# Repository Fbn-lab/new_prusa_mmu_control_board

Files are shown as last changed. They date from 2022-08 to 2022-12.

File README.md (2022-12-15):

(语言 language) : [CN](https://github.com/fBn0523/new_prusa_mmu_control_board/blob/main/README.md)|[EN](https://github.com/fBn0523/new_prusa_mmu_control_board/blob/main/README_EN.md)

# ENDER3多色改装方案
# new_prusa_mmu_hardware
平替原版mmu2主板,单板只需要约100(CNY)\
  PCB_V4.1|参数|类型
  --------|---|---
  电源|12~24V|/
  串口|5V/3.3V|/
  FINDA传感器|12~24V|三线PNP常开
电机驱动|/|TMC2130

直插mks主板，兼容更多打印机。\
无论你的打印机是否来自prusa生产，只要主板拥有一个空闲的串口和两个gpio,使用marlin固件。都可以使用mmu换料器。
# image
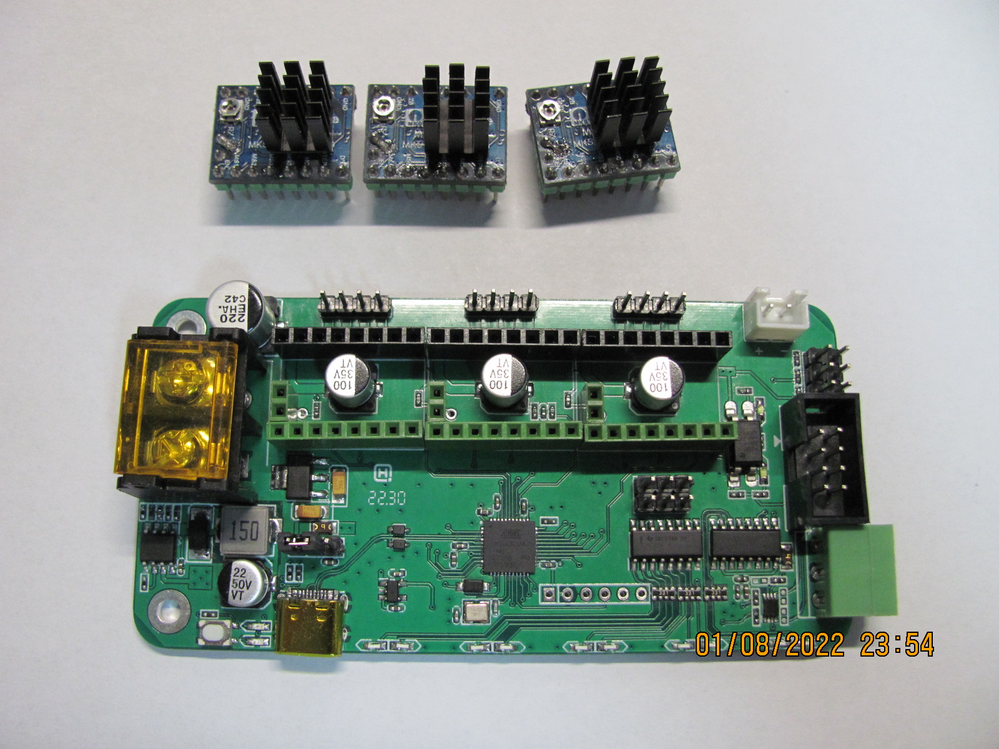
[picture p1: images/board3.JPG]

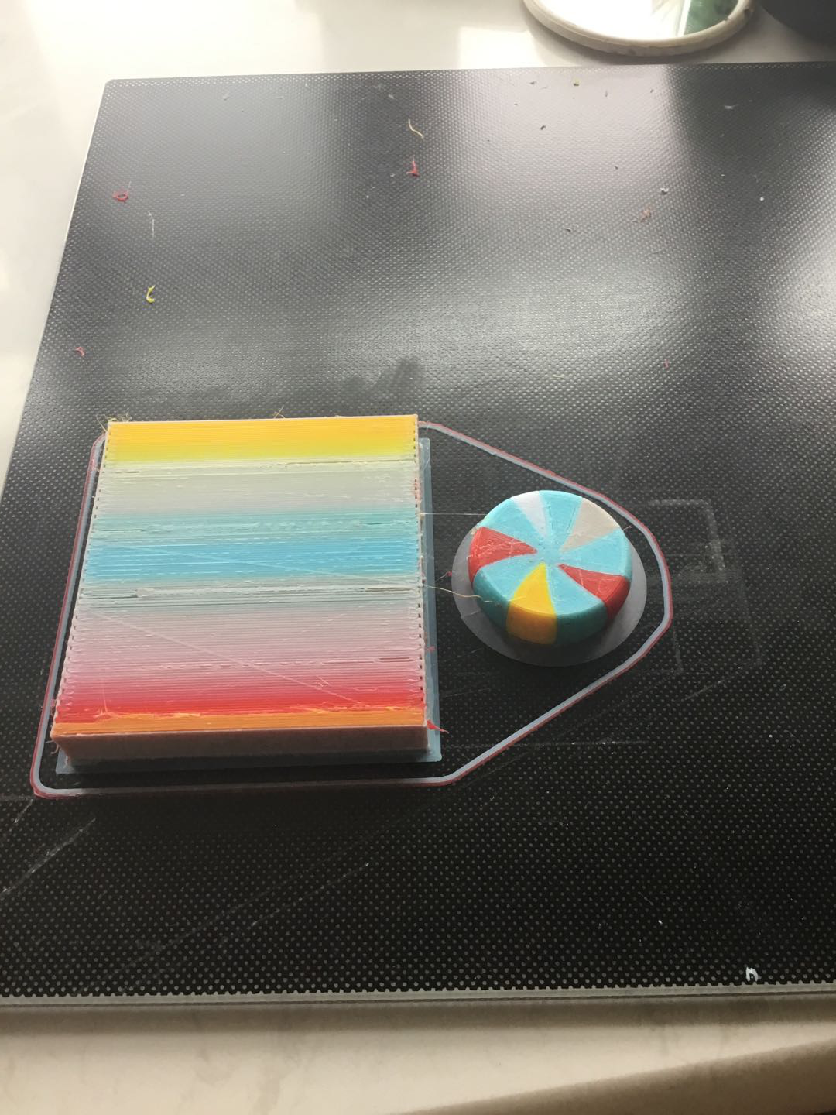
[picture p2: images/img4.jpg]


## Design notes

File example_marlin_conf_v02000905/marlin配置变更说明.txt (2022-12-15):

/**********************************************************************/
#define EXTRUDERS 5//部分主板不能设置5个挤出机,忽略错误即可
/**********************************************************************/
#define MMU_MODEL PRUSA_MMU2   
/**********************************************************************/
#define FILAMENT_RUNOUT_SENSOR  //断料传感器使能
#if ENABLED(FILAMENT_RUNOUT_SENSOR)
  #define FIL_RUNOUT_ENABLED_DEFAULT true 
  #define NUM_RUNOUT_SENSORS   1           

  #define FIL_RUNOUT_STATE     HIGH        
  #define FIL_RUNOUT_PULLUP       
/**********************************************************************/

#define NOZZLE_PARK_FEATURE//用于设置mmu停止时喷头位置

#if ENABLED(NOZZLE_PARK_FEATURE)
  // Specify a park position as { X, Y, Z_raise }
  #define NOZZLE_PARK_POINT { (X_MIN_POS + 10), (Y_MIN_POS + 10), 20 }
  #define NOZZLE_PARK_MOVE          0   // Park motion: 0 = XY Move, 1 = X Only, 2 = Y Only, 3 = X before Y, 4 = Y before X
  #define NOZZLE_PARK_Z_RAISE_MIN   2   // (mm) Always raise Z by at least this distance
  #define NOZZLE_PARK_XY_FEEDRATE 100   // (mm/s) X and Y axes feedrate (also used for delta Z axis)
  #define NOZZLE_PARK_Z_FEEDRATE    5   // (mm/s) Z axis feedrate (not used for delta printers)
#endif       

#define ADVANCED_PAUSE_FEATURE//多色上下料速度长度设置
#if ENABLED(ADVANCED_PAUSE_FEATURE)
  #define PAUSE_PARK_RETRACT_FEEDRATE         60  // (mm/s) Initial retract feedrate.
  #define PAUSE_PARK_RETRACT_LENGTH            2  // (mm) Initial retract.
                                                  // This short retract is done immediately, before parking the nozzle.
  #define FILAMENT_CHANGE_UNLOAD_FEEDRATE     10  // (mm/s) Unload filament feedrate. This can be pretty fast.
  #define FILAMENT_CHANGE_UNLOAD_ACCEL        25  // (mm/s^2) Lower acceleration may allow a faster feedrate.
  #define FILAMENT_CHANGE_UNLOAD_LENGTH      100  // (mm) The length of filament for a complete unload.
                                                  //   For Bowden, the full length of the tube and nozzle.
                                                  //   For direct drive, the full length of the nozzle.
                                                  //   Set to 0 for manual unloading.
  #define FILAMENT_CHANGE_SLOW_LOAD_FEEDRATE   6  // (mm/s) Slow move when starting load.
  #define FILAMENT_CHANGE_SLOW_LOAD_LENGTH     0  // (mm) Slow length, to allow time to insert material.
                                                  // 0 to disable start loading and skip to fast load only
  #define FILAMENT_CHANGE_FAST_LOAD_FEEDRATE   6  // (mm/s) Load filament feedrate. This can be pretty fast.
  #define FILAMENT_CHANGE_FAST_LOAD_ACCEL     25  // (mm/s^2) Lower acceleration may allow a faster feedrate.
  #define FILAMENT_CHANGE_FAST_LOAD_LENGTH    90  // (mm) Load length of filament, from extruder gear to nozzle.
                                                  //   For Bowden, the full length of the tube and nozzle.
                                                  //   For direct drive, the full length of the nozzle.
  //#define ADVANCED_PAUSE_CONTINUOUS_PURGE       // Purge continuously up to the purge length until interrupted.
  #define ADVANCED_PAUSE_PURGE_FEEDRATE        3  // (mm/s) Extrude feedrate (after loading). Should be slower than load feedrate.
  #define ADVANCED_PAUSE_PURGE_LENGTH         25  // (mm) Length to extrude after loading.
                                                  //   Set to 0 for manual extrusion.
                                                  //   Filament can be extruded repeatedly from the Filament Change menu
                                                  //   until extrusion is consistent, and to purge old filament.
  #define ADVANCED_PAUSE_RESUME_PRIME          0  // (mm) Extra distance to prime nozzle after returning from park.
  //#define ADVANCED_PAUSE_FANS_PAUSE             // Turn off print-cooling fans while the machine is paused.

                                                  // Filament Unload does a Retract, Delay, and Purge first:
  #define FILAMENT_UNLOAD_PURGE_RETRACT       13  // (mm) Unload initial retract length.
  #define FILAMENT_UNLOAD_PURGE_DELAY       5000  // (ms) Delay for the filament to cool after retract.
  #define FILAMENT_UNLOAD_PURGE_LENGTH         8  // (mm) An unretract is done, then this length is purged.
  #define FILAMENT_UNLOAD_PURGE_FEEDRATE      25  // (mm/s) feedrate to purge before unload

  #define PAUSE_PARK_NOZZLE_TIMEOUT           45  // (seconds) Time limit before the nozzle is turned off for safety.
  #define FILAMENT_CHANGE_ALERT_BEEPS         10  // Number of alert beeps to play when a response is needed.
  #define PAUSE_PARK_NO_STEPPER_TIMEOUT           // Enable for XYZ steppers to stay powered on during filament change.
  //#define FILAMENT_CHANGE_RESUME_ON_INSERT      // Automatically continue / load filament when runout sensor is triggered again.
  //#define PAUSE_REHEAT_FAST_RESUME              // Reduce number of waits by not prompting again post-timeout before continuing.

  //#define PARK_HEAD_ON_PAUSE                    // Park the nozzle during pause and filament change.
  //#define HOME_BEFORE_FILAMENT_CHANGE           // If needed, home before parking for filament change

  #define FILAMENT_LOAD_UNLOAD_GCODES           // Add M701/M702 Load/Unload G-codes, plus Load/Unload in the LCD Prepare menu.
  //#define FILAMENT_UNLOAD_ALL_EXTRUDERS         // Allow M702 to unload all extruders above a minimum target temp (as set by M302)
#endif 
/**********************************************************************/
/**
 * Průša Multi-Material Unit (MMU)
 * Enable in Configuration.h
 *
 * These devices allow a single stepper driver on the board to drive
 * multi-material feeders with any number of stepper motors.
 */
#if HAS_PRUSA_MMU1
  /**
   * This option only allows the multiplexer to switch on tool-change.
   * Additional options to configure custom E moves are pending.
   *
   * Override the default DIO selector pins here, if needed.
   * Some pins files may provide defaults for these pins.
   */
  //#define E_MUX0_PIN 40  // Always Required
  //#define E_MUX1_PIN 42  // Needed for 3 to 8 inputs
  //#define E_MUX2_PIN 44  // Needed for 5 to 8 inputs
#elif HAS_PRUSA_MMU2
  // Serial port used for communication with MMU2.
  #define MMU2_SERIAL Serial2//串口号 (BOARD_TRIGORILLA_13 选串口3)(MKS tinybee选串口二)

  // Use hardware reset for MMU if a pin is defined for it
  #define MMU2_RST_PIN 2//复位引脚

  // Enable if the MMU2 has 12V stepper motors (MMU2 Firmware 1.0.2 and up)
  #define MMU2_MODE_12V//供电是否12V

  // G-code to execute when MMU2 F.I.N.D.A. probe detects filament runout
  #define MMU2_FILAMENT_RUNOUT_SCRIPT "M600"

  // Add an LCD menu for MMU2
  #define MMU2_MENUS
  #if EITHER(MMU2_MENUS, HAS_PRUSA_MMU2S)
    // Settings for filament load / unload from the LCD menu.
    // This is for Průša MK3-style extruders. Customize for your hardware.
    #define MMU2_FILAMENTCHANGE_EJECT_FEED 80.0
    #define MMU2_LOAD_TO_NOZZLE_SEQUENCE \
      {  7.2, 1145 }, \
      { 14.4,  871 }, \
      { 36.0, 1393 }, \
      { 14.4,  871 }, \
      { 50.0,  198 }

    #define MMU2_RAMMING_SEQUENCE \
      {   1.0, 1000 }, \
      {   1.0, 1500 }, \
      {   2.0, 2000 }, \
      {   1.5, 3000 }, \
      {   2.5, 4000 }, \
      { -15.0, 5000 }, \
      { -14.0, 1200 }, \
      {  -6.0,  600 }, \
      {  10.0,  700 }, \
      { -10.0,  400 }, \
      { -50.0, 2000 }
  #endif

  /**
   * Using a sensor like the MMU2S
   * This mode requires a MK3S extruder with a sensor at the extruder idler, like the MMU2S.
   * See https://help.prusa3d.com/en/guide/3b-mk3s-mk2-5s-extruder-upgrade_41560, step 11
   */
  #if HAS_PRUSA_MMU2S
    #define MMU2_C0_RETRY   5             // Number of retries (total time = timeout*retries)

    #define MMU2_CAN_LOAD_FEEDRATE 500    // (mm/min)
    #define MMU2_CAN_LOAD_SEQUENCE \
      {  0.1, MMU2_CAN_LOAD_FEEDRATE }, \
      {  50, MMU2_CAN_LOAD_FEEDRATE }, \
      { -42.0, MMU2_CAN_LOAD_FEEDRATE }

    #define MMU2_CAN_LOAD_RETRACT   6.0   // (mm) Keep under the distance between Load Sequence values
    #define MMU2_CAN_LOAD_DEVIATION 0.8   // (mm) Acceptable deviation

    #define MMU2_CAN_LOAD_INCREMENT 0.2   // (mm) To reuse within MMU2 module
    #define MMU2_CAN_LOAD_INCREMENT_SEQUENCE \
      { -MMU2_CAN_LOAD_INCREMENT, MMU2_CAN_LOAD_FEEDRATE }

  #else

    /**
     * MMU1 Extruder Sensor
     *
     * Support for a Průša (or other) IR Sensor to detect filament near the extruder
     * and make loading more reliable. Suitable for an extruder equipped with a filament
     * sensor less than 38mm from the gears.
     *
     * During loading the extruder will stop when the sensor is triggered, then do a last
     * move up to the gears. If no filament is detected, the MMU2 can make some more attempts.
     * If all attempts fail, a filament runout will be triggered.
     */
    #define MMU_EXTRUDER_SENSOR
    #if ENABLED(MMU_EXTRUDER_SENSOR)
      #define MMU_LOADING_ATTEMPTS_NR 5 // max. number of attempts to load filament if first load fail
    #endif

  #endif

  //#define MMU2_DEBUG  // Write debug info to serial output

#endif // HAS_PRUSA_MMU2

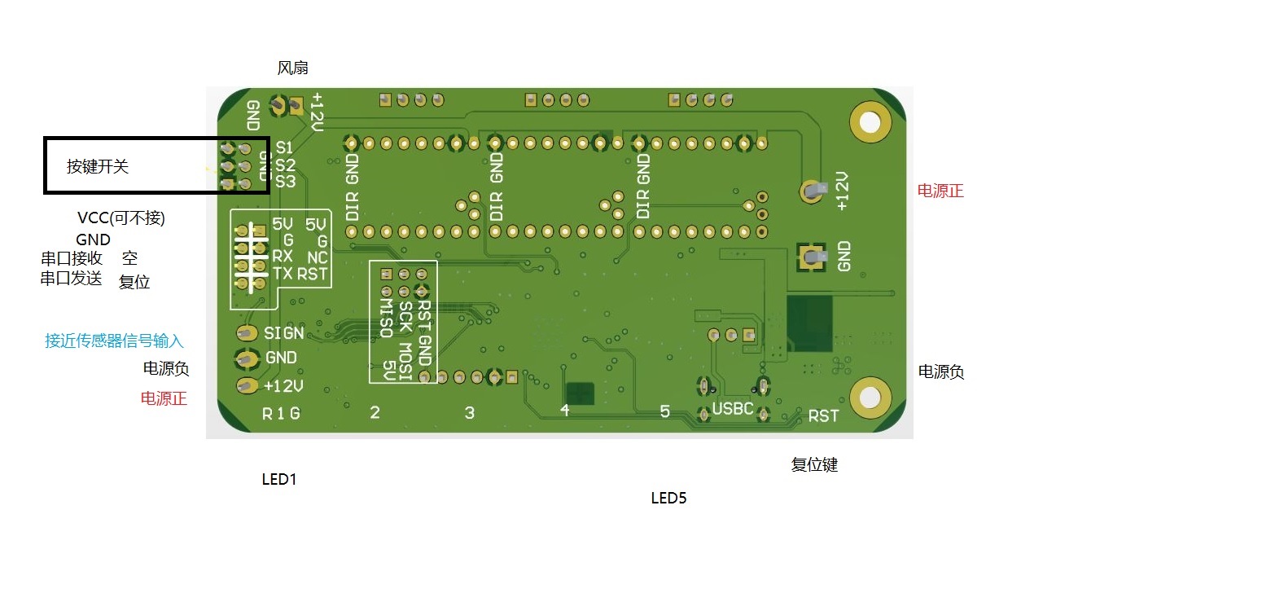
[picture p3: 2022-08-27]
hardware/mother_board/板卡底面示意图.JPG

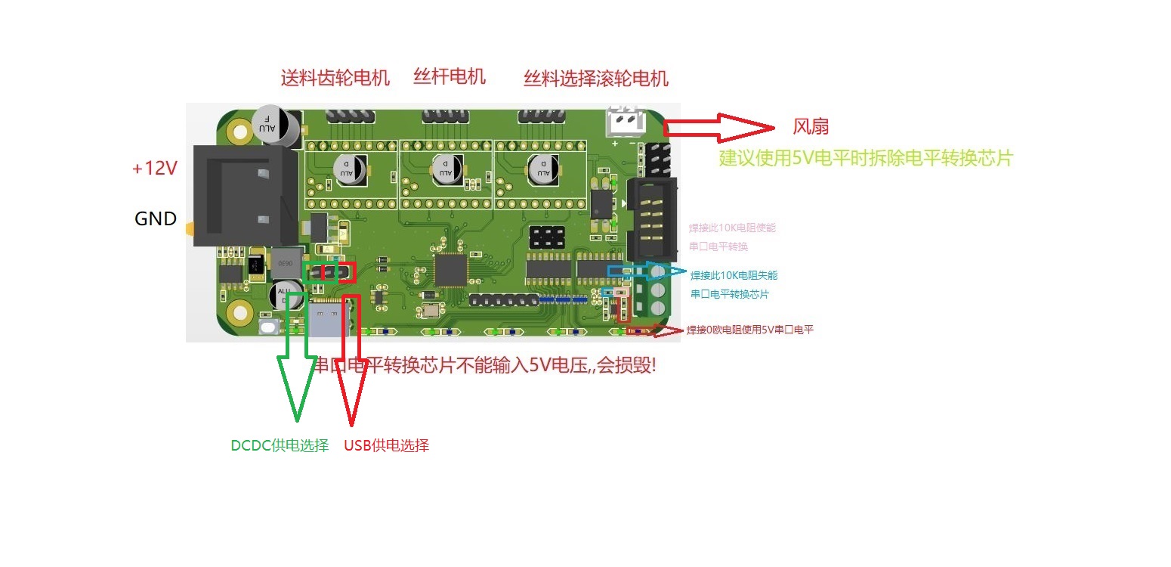
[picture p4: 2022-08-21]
hardware/mother_board/接线示意图_V3.4_HQPCB__20_30.jpg

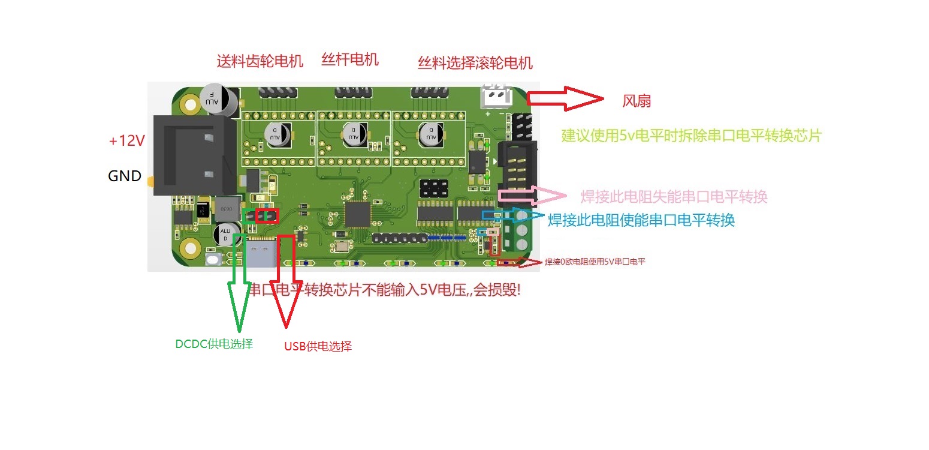
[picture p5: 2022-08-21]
hardware/mother_board/接线示意图_V4.1.jpg

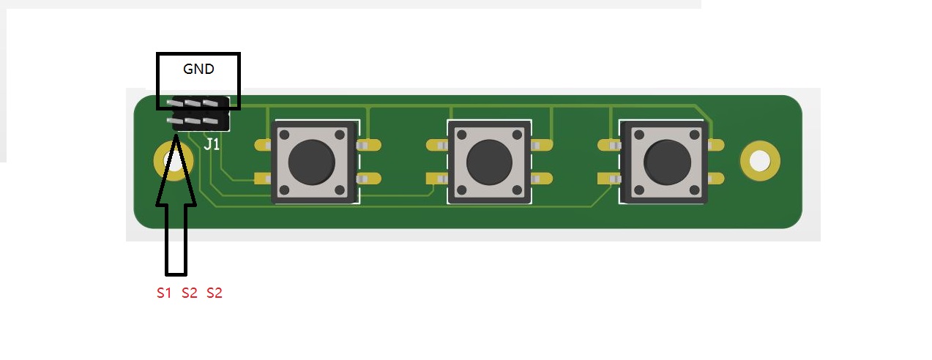
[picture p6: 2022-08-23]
hardware/switch_board/接线示意图.JPG

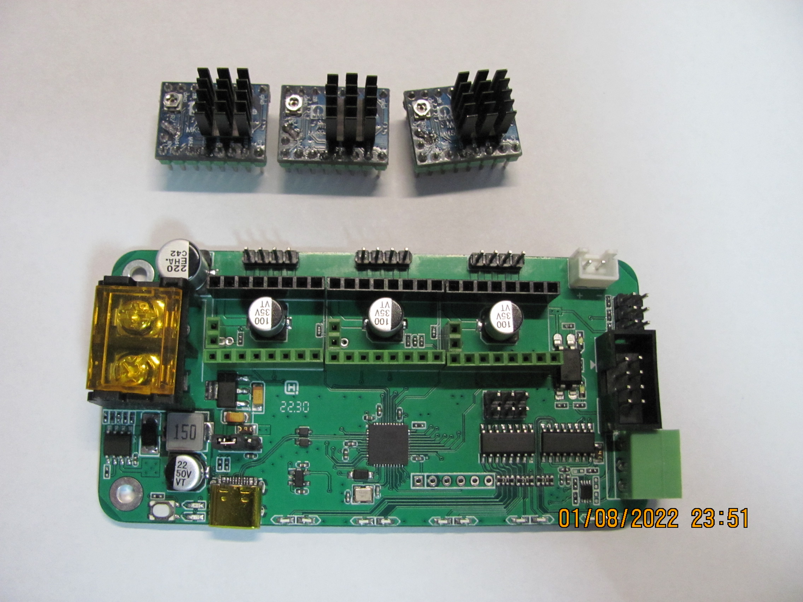
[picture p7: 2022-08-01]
images/board2.JPG

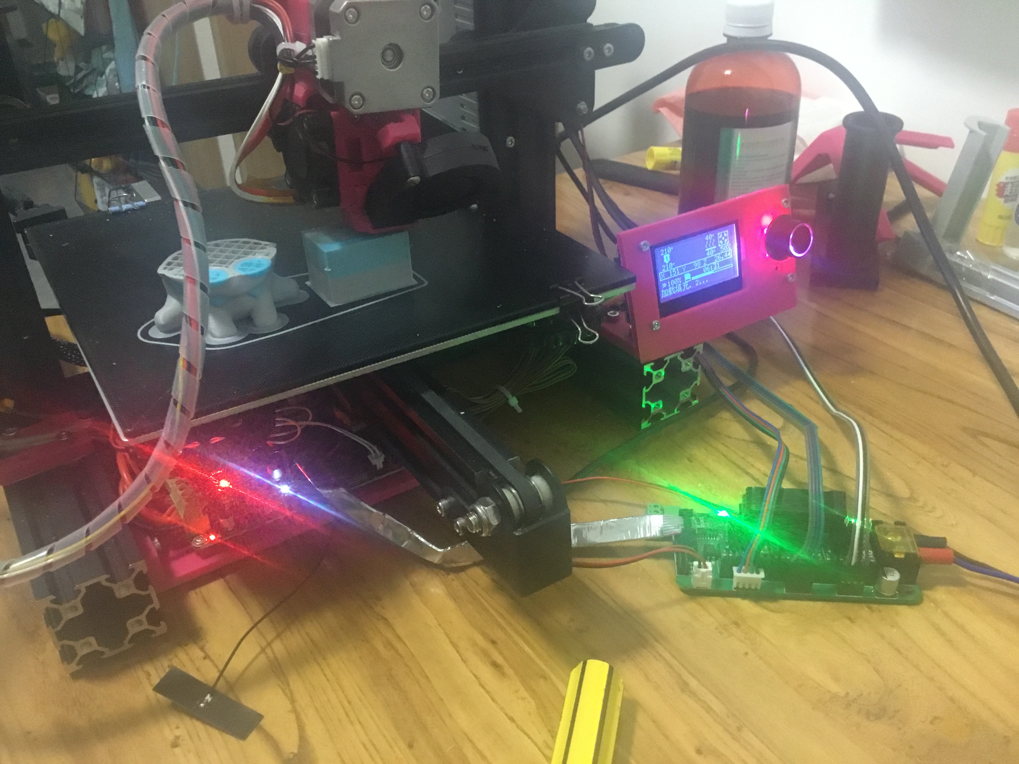
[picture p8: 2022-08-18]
images/img.jpg

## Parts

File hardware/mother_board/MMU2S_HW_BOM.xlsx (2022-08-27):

Comment | 厂家 | 立创商城产品号 | Description | 元件号 | 封装 | LibRef | 数量 | 特别注意连接器间距,电容耐压.器件高温性能
10uF |  |  | 无极性电容 | C1, C10, C12, C14 | 0402C | CAP | 4
100nF |  |  | 无极性电容 | C2, C4, C7, C9, C11, C13, C15 | 0402C | CAP | 7
150pF |  |  | 无极性电容 | C3 | 0402C | CAP | 1
1uF |  |  | 无极性电容 | C5, C16, C17 | 0402C | CAP | 3
12pF |  |  | 无极性电容 | C6, C8 | 0402C | CAP | 2
SS34 | 萨科微 | C77336 | 肖特基二极管 | D1 | SMA/DO-214AC | DIODE SCHOTTKY | 1
LED |  |  | LED灯 | D2,D3,D4,D5,D6,D7,D8, D9, D10, D11,D12,D13 D14, D16, | LED-0603 | 注意颜色！ | 14
DIODE | 杨杰 | C961806 | 普通二极管 | D15 | SOD-123 | DIODE | 1
SMBJ5 | 美台 | C460454 | TVS二极管5V | D17, D18 | SOD-323 | DIODE ZENER | 2
100uF | 建议车规级,耐高温 |  | 贴片电解电容 | EC1, EC2, EC3 | SMD-EC6.3X6.3X10 | SMD_ECAP | 3
22uF |  |  | 贴片电解电容 | EC4 | SMD-EC6.3X6.3X10 | SMD_ECAP | 1
220uF | Panasonic | C336329 | 贴片电解电容 | EC5 | SMD-EC8X8X10 | SMD_ECAP | 1
ATMEGA32U4RC-MU | microchip |  | 单片机 | IC1 | QFN50P700X700X100-45N-D | ATMEGA32U4RC-MU | 1
74HC595D | Ti |  | 8位移位寄存器 | IC2, IC3 | SOIC127P600X175-16N | 74HC595D | 2
MP1584EN-LF |  |  | DCDC芯片 | IC4 | SOIC127P600X170-9N | MP1584EN-LF | 1
AMS1117-5 | UMW | C347223 | 低压差线性稳压器LDO | IC5 | SOT229P700X180-4N | AMS1117 | 1
ME6211 | 南京微盟 | C82942 | 低压差线性稳压器LDO | IC6 | SOT95P280X145-5N | ME6211 | 1
TXS0102DCUR | TI |  | 电平转换芯片 | IC7 | SOP50P310X90-8N | TXS0102DCUR | 1
MOTOR1 |  |  | 排针 | J1,J2,J3 | Pin HDR1X4/2.54mm-S | Pin HDR1X4 | 3
HB9500-9.5-2P |  |  | 接线端子 | J4 | SHDR2W140P0X950_1X2_2055X1800X1440P | HB9500-9.5-2P接线端子注意间距！ | 1
KF128-3P |  |  | 接线端子 | J5 | KF128-3.81-3P | KF128-3P | 1
Pin HDR1X6 |  |  | 排针 | J6 | Pin HDR1X6/2.54mm-S | Pin HDR1X6 | 1
IDC-8P |  |  | 牛角坐 | J8 | IDC2.54-8P | IDC-8P | 1
Pin HDR2X3 |  |  | 排针 | J9, J10 | Pin HDR2X3/2.54mm-S | Pin HDR2X3 | 2
Pin HDR1X3 |  |  | 排针 | J11 | Pin HDR1X3/2.54mm-S | Pin HDR1X3 | 1
switch_3*4*2.5mm |  |  | 微动开关 | K4 | switch_3*4*2.5mm | switch_3*4*2.5mm | 1
15uH |  |  | 贴片电感 | L1 | 0630L | INDUCTOR | 1
F0.5A |  |  | 保险丝 | L2 | 0805L | INDUCTOR | 1
F1.1A |  |  | 保险丝 | L4 | 0805L | INDUCTOR | 1
PC817 | UMW |  | 线性光耦 | OC1 | SMD_PC817 | PC817 | 1
10K | 厚声 | C25744 | 电阻 | R1, R2, R3, R6, R11, R16, R17, R23, R24, R25 | 0402R | RES | 10
100K |  |  | 电阻 | R4, R5 | 0402R | RES | 2
43K |  |  | 电阻 | R7 | 0402R | RES | 1
5K |  |  | 电阻 | R8 | 0402R | RES | 1
1K |  |  | 电阻 | R9, R10, R19 | 0402R | RES | 3
15K |  |  | 电阻 | R12 | 0402R | RES | 1
1R5K |  |  | 电阻 | R13, R14 | 0402R | RES | 2
1.5K |  |  | 电阻 | R15 | 0402R | RES | 1
2.7K |  |  | 电阻 | R18 | 0402R | RES | 1
100R |  |  | 电阻 | R20, R21 | 0402R | RES | 2
510R |  |  | 电阻 | R22 | 0402R | RES | 1
0R |  |  | 电阻 | R26, R27 | 0402R | RES | 2
330R*4 |  |  | 排阻 | RN1, RN2, RN3 | ACASA100021000P100 | ACASA1000S1000P1AT | 3
10uF | AVX | C7171 | 钽电容 | TC1, TC2 | TAJ-A/3216 | TCAP | 2
TMC2130 |  |  | 电机驱动 | U1, U2, U4 | TMC2130 | TMC2130 | 3
TYPE-C | 金航标 | C709357 | usb连接器 | U3 | USB-C-SMD_TYPEC-304-BCP16 | TYPEC-304-BCP16 | 1
16MHZ | 建议车规级,耐高温 |  | 4脚无源晶振 | X1 | OSC 3225-4P | XTAL-4P | 1
XH2 |  |  | 胶壳端子 | XH1 | XH2/2.54mm/180 | XH2 | 1
闲杂项 | 跳线帽x1 | 2孔排母x3 | 8孔排母绿色x3 | 8孔排母黑色x3 | 12mm微动开关x3 | 主板到mmu控制板排线x1 | 8mm直径接近传感器（电感式）PNP常开 |  | 7mm钢珠x1

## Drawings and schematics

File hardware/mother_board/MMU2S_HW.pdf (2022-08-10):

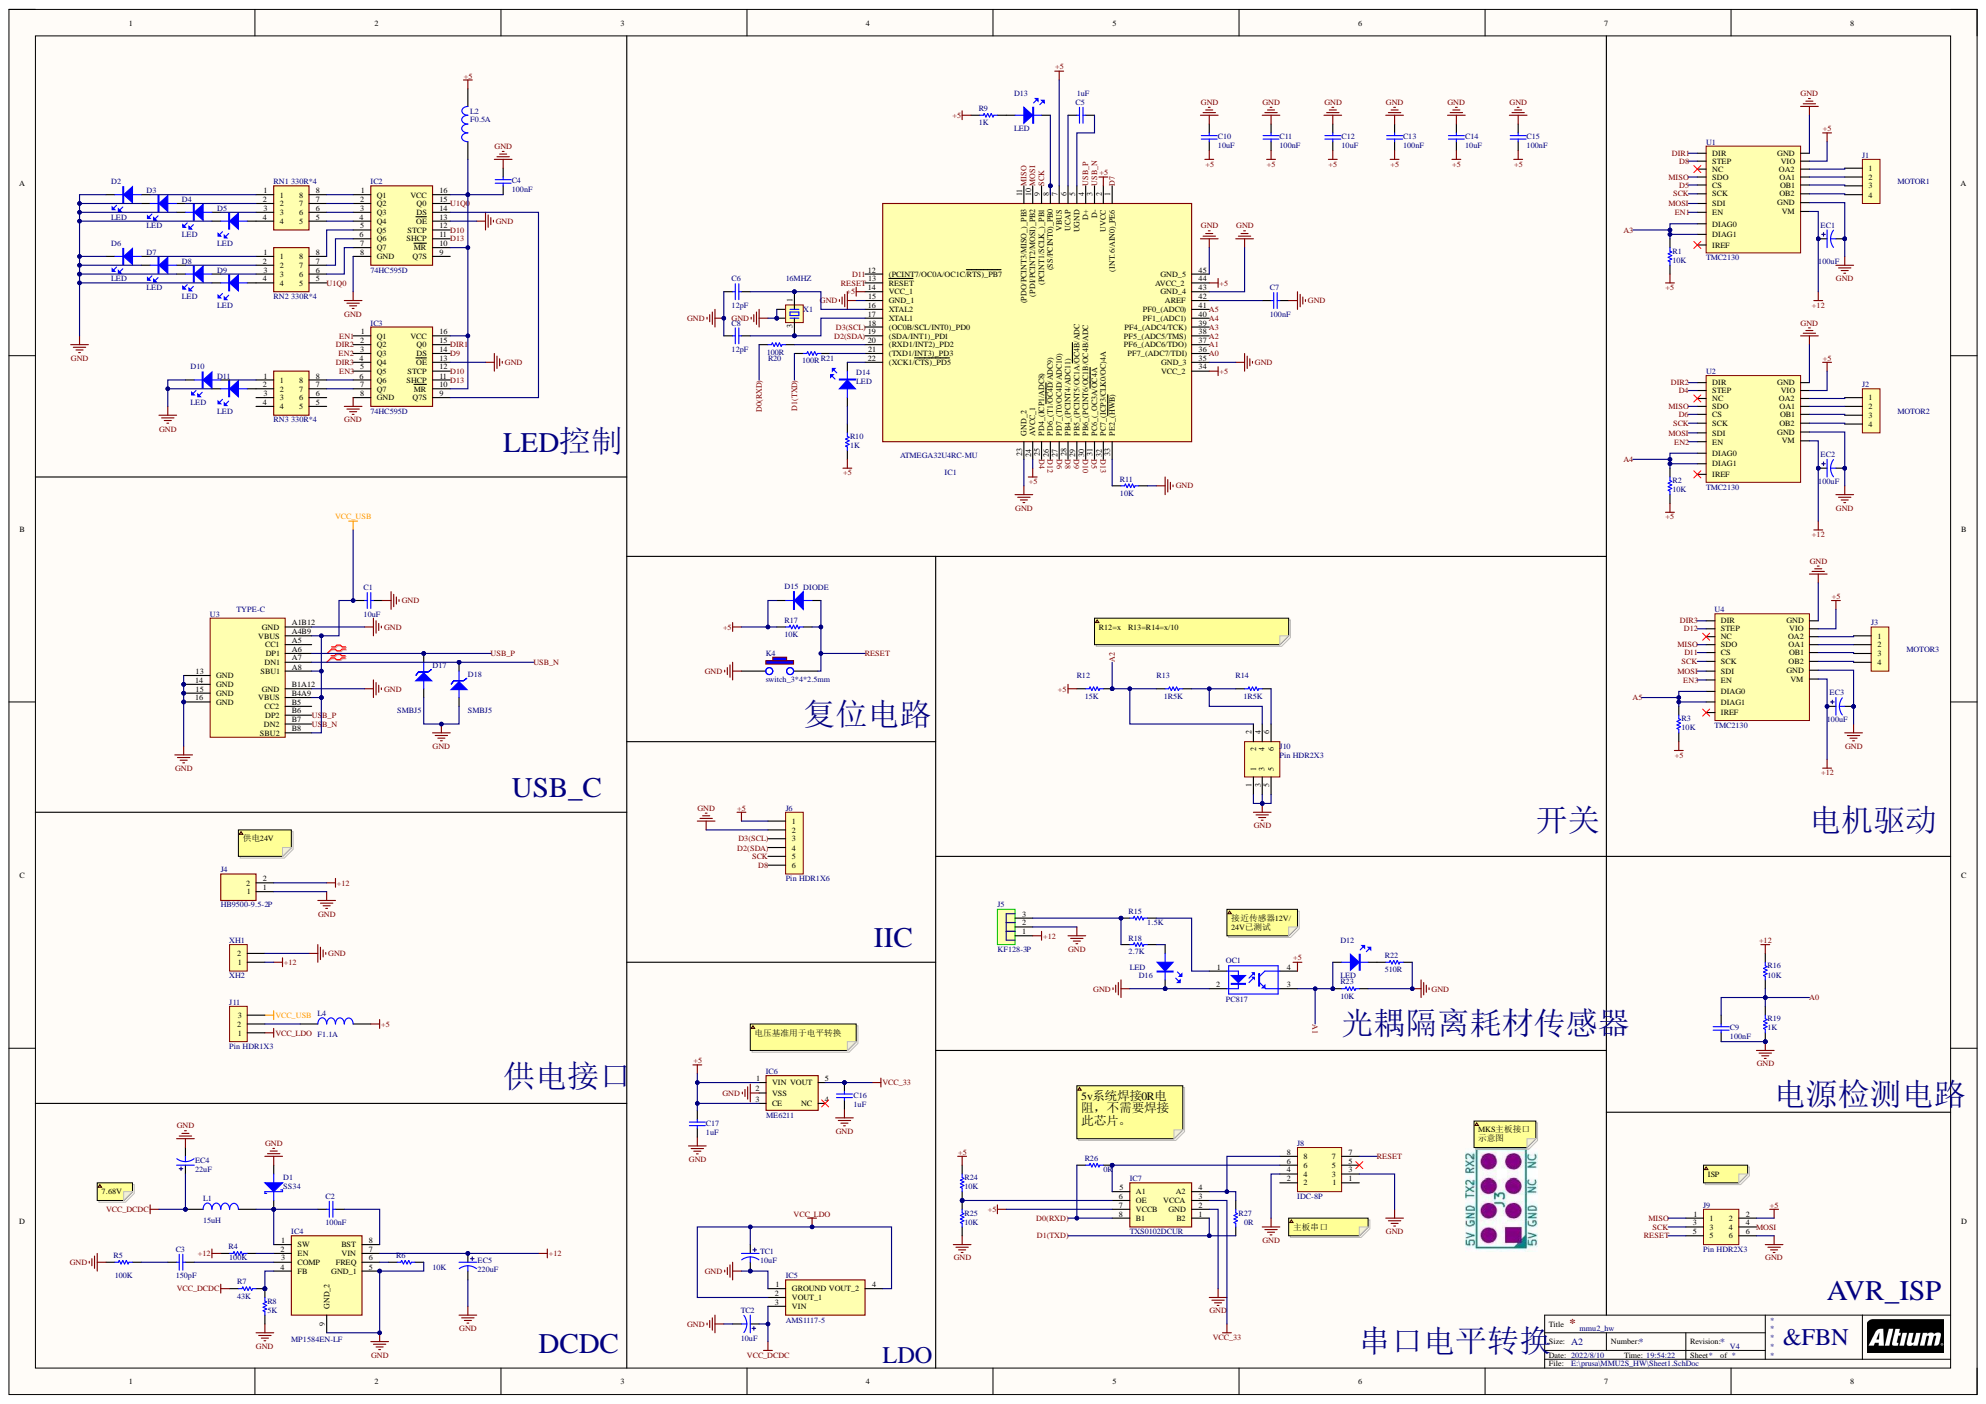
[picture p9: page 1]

(INT.6/AIN0)_PE6 1 UVCC 2 D- 3 D+ 4 UGND 5 UCAP 6 VBUS 7 (SS/PCINT0)_PB0 8 (PCINT1/SCLK_)_PB1 9 (PDI/PCINT2/MOSI)_PB2 10 (PDO/PCINT3/MISO_)_PB3 11

_(HWB) 33 PC7_(ICP3/CLK0/OC)4A 32 PC6_(_OC3A/OC4A 31 PB6_(PCINT6/OC1B/OC4B/ADC 30 PB5_(PCINT5/OC1A/OC4B/ADC 29 PB4_(PCINT4/ADC11) 28 PD7_(T0/OC4D/ADC10) 27 PD6_(T1/OC4D/ADC9) 26 PD4_(ICP1/ADC8) 25 AVCC_1 24 GND_2 23

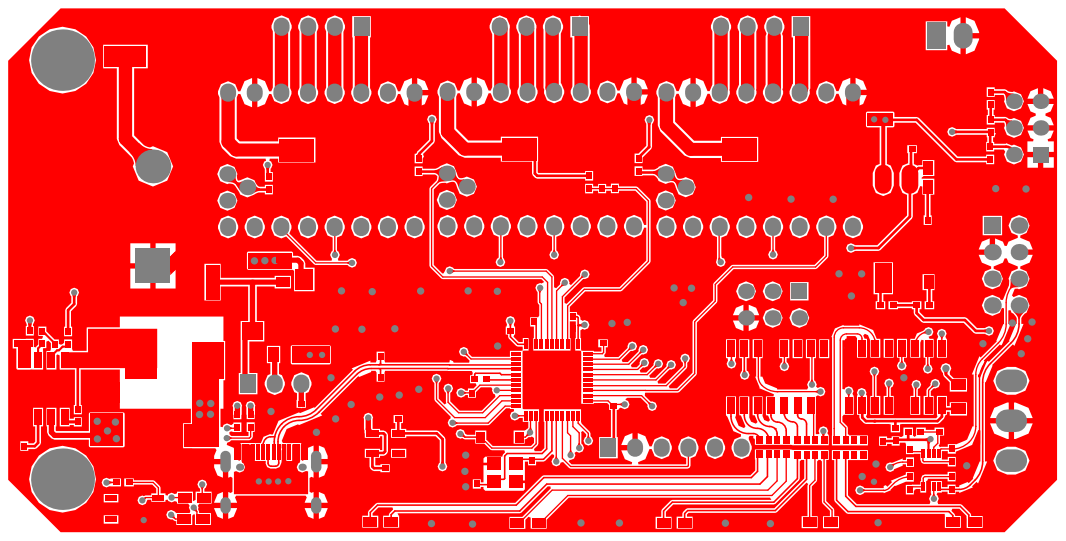
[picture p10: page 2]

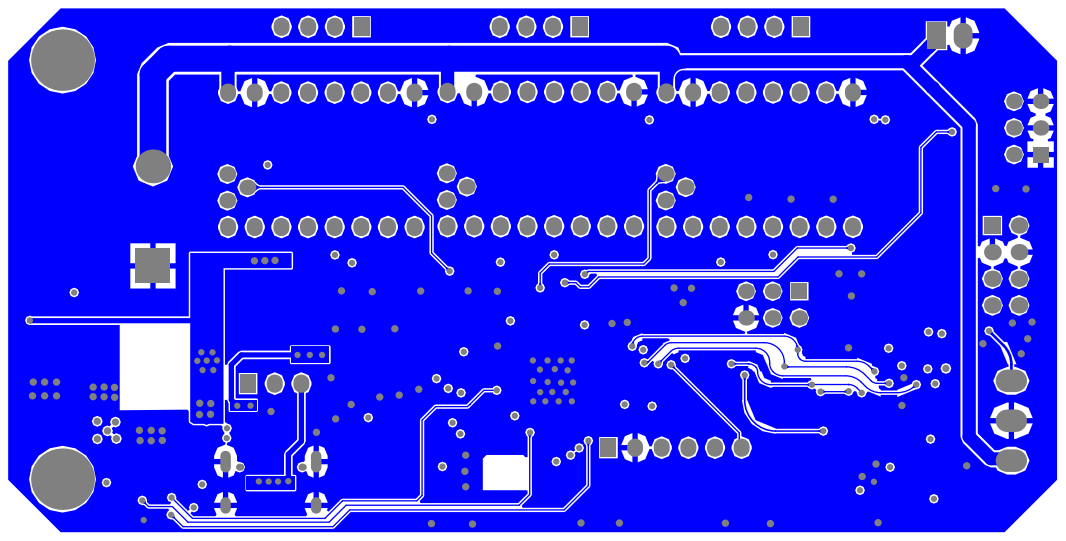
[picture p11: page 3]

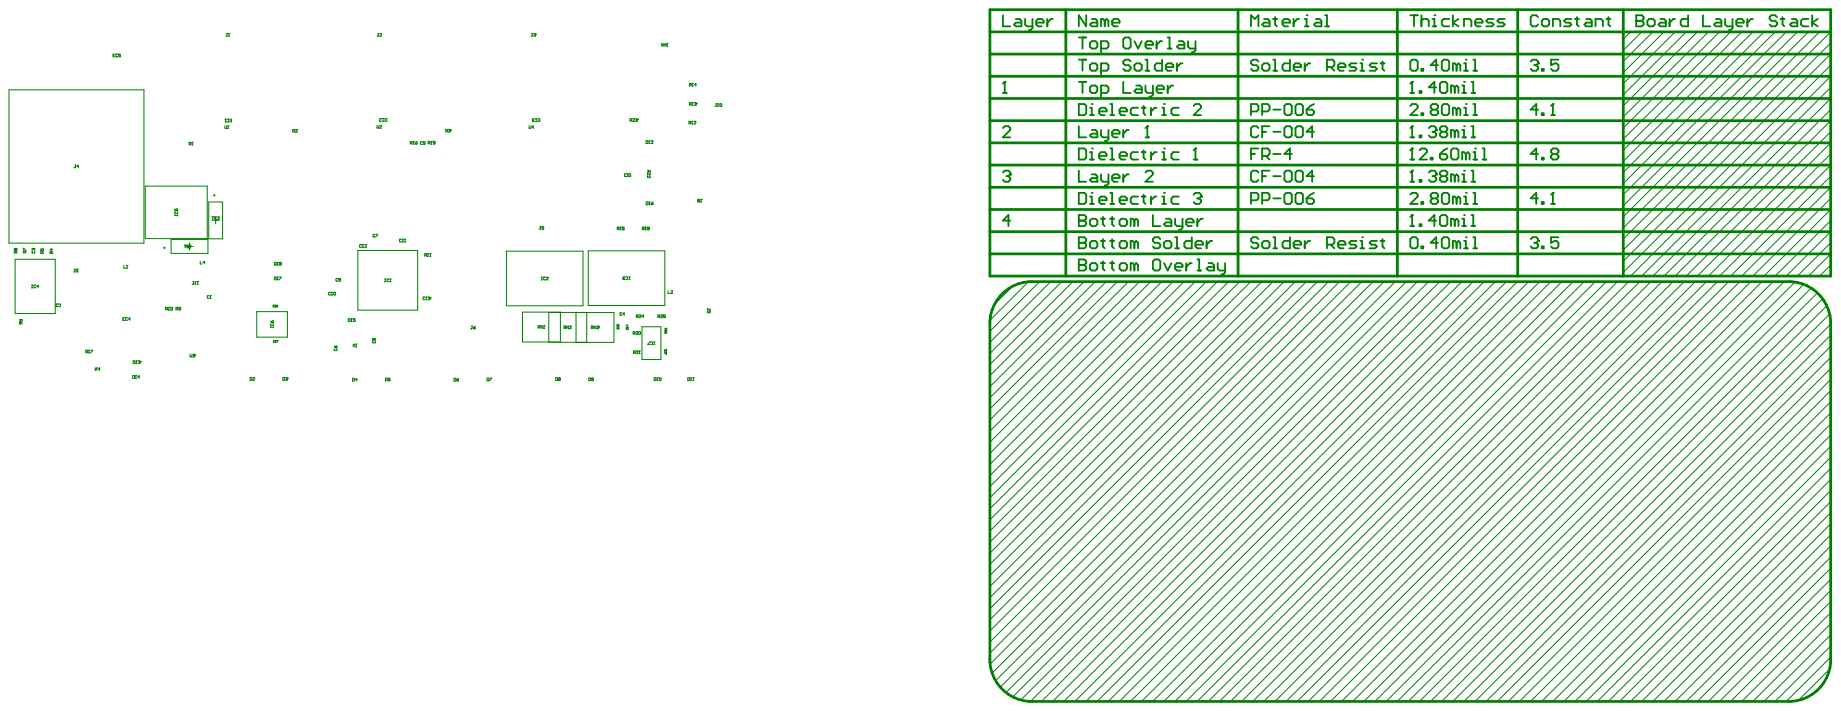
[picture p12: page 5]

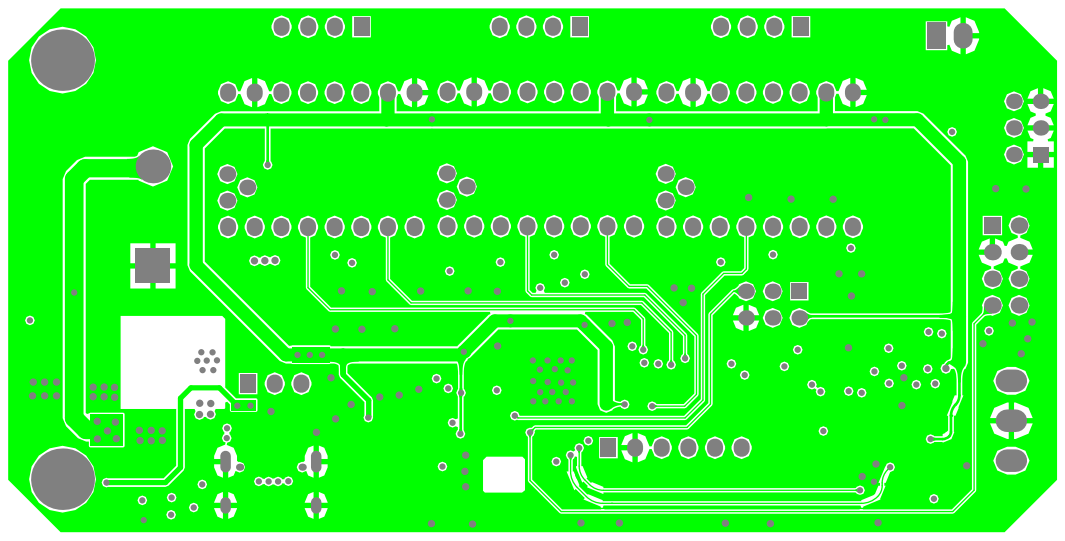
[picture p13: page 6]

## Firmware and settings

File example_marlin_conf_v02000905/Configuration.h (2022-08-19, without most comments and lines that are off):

#pragma once
#define CONFIGURATION_H_VERSION 02000905
#define STRING_CONFIG_H_AUTHOR "(none, default config)" // Who made the changes.
#define SHOW_BOOTSCREEN
  #define MOTHERBOARD BOARD_MKS_TINYBEE
#define SERIAL_PORT 0
#define BAUDRATE 115200
#define SERIAL_PORT_2 -1
#define BAUDRATE_2 115200   // Enable to override BAUDRATE
#define CUSTOM_MACHINE_NAME "ENDER3++"
#define MACHINE_UUID "mmu_hw_v3.4-sw_V1.06-marlin_v2.9.5"
#define X_DRIVER_TYPE  LV8729
#define Y_DRIVER_TYPE  LV8729
#define Z_DRIVER_TYPE  LV8729
#define E0_DRIVER_TYPE A4988
#define EXTRUDERS 5
#define DEFAULT_NOMINAL_FILAMENT_DIA 1.75
#define MMU_MODEL PRUSA_MMU2
#define PSU_CONTROL
#define PSU_NAME "Power Supply"
  #define PSU_ACTIVE_STATE HIGH      // Set 'LOW' for ATX, 'HIGH' for X-Box
  #define  PS_ON_PIN 150
  #define POWER_OFF_TIMER               // Enable M81 D<seconds> to power off after a delay
#define TEMP_SENSOR_0 1
#define TEMP_SENSOR_1 0
#define TEMP_SENSOR_2 0
#define TEMP_SENSOR_3 0
#define TEMP_SENSOR_4 0
#define TEMP_SENSOR_5 0
#define TEMP_SENSOR_6 0
#define TEMP_SENSOR_7 0
#define TEMP_SENSOR_BED 1
#define TEMP_SENSOR_PROBE 0
#define TEMP_SENSOR_CHAMBER 0
#define TEMP_SENSOR_COOLER 0
#define TEMP_SENSOR_BOARD 0
#define TEMP_SENSOR_REDUNDANT 0
#define DUMMY_THERMISTOR_998_VALUE  25
#define DUMMY_THERMISTOR_999_VALUE 100
#define TEMP_RESIDENCY_TIME         10  // (seconds) Time to wait for hotend to "settle" in M109
#define TEMP_WINDOW                  1  // (°C) Temperature proximity for the "temperature reached" timer
#define TEMP_HYSTERESIS              3  // (°C) Temperature proximity considered "close enough" to the target
#define TEMP_BED_RESIDENCY_TIME     10  // (seconds) Time to wait for bed to "settle" in M190
#define TEMP_BED_WINDOW              1  // (°C) Temperature proximity for the "temperature reached" timer
#define TEMP_BED_HYSTERESIS          3  // (°C) Temperature proximity considered "close enough" to the target
#define TEMP_CHAMBER_RESIDENCY_TIME 10  // (seconds) Time to wait for chamber to "settle" in M191
#define TEMP_CHAMBER_WINDOW          1  // (°C) Temperature proximity for the "temperature reached" timer
#define TEMP_CHAMBER_HYSTERESIS      3  // (°C) Temperature proximity considered "close enough" to the target
#if TEMP_SENSOR_REDUNDANT
  #define TEMP_SENSOR_REDUNDANT_SOURCE    E1  // The sensor that will provide the redundant reading.
  #define TEMP_SENSOR_REDUNDANT_TARGET    E0  // The sensor that we are providing a redundant reading for.
  #define TEMP_SENSOR_REDUNDANT_MAX_DIFF  10  // (°C) Temperature difference that will trigger a print abort.
#endif
#define HEATER_0_MINTEMP   5
#define HEATER_1_MINTEMP   5
#define HEATER_2_MINTEMP   5
#define HEATER_3_MINTEMP   5
#define HEATER_4_MINTEMP   5
#define HEATER_5_MINTEMP   5
#define HEATER_6_MINTEMP   5
#define HEATER_7_MINTEMP   5
#define BED_MINTEMP        5
#define CHAMBER_MINTEMP    5
#define HEATER_0_MAXTEMP 275
#define HEATER_1_MAXTEMP 275
#define HEATER_2_MAXTEMP 275
#define HEATER_3_MAXTEMP 275
#define HEATER_4_MAXTEMP 275
#define HEATER_5_MAXTEMP 275
#define HEATER_6_MAXTEMP 275
#define HEATER_7_MAXTEMP 275
#define BED_MAXTEMP      100
#define CHAMBER_MAXTEMP  60
#define HOTEND_OVERSHOOT 15   // (°C) Forbid temperatures over MAXTEMP - OVERSHOOT
#define BED_OVERSHOOT    10   // (°C) Forbid temperatures over MAXTEMP - OVERSHOOT
#define COOLER_OVERSHOOT  2   // (°C) Forbid temperatures closer than OVERSHOOT
#define PIDTEMP          // See the PID Tuning Guide at https://reprap.org/wiki/PID_Tuning
#define BANG_MAX 255     // Limits current to nozzle while in bang-bang mode; 255=full current
#define PID_MAX BANG_MAX // Limits current to nozzle while PID is active (see PID_FUNCTIONAL_RANGE below); 255=full current
#define PID_K1 0.95      // Smoothing factor within any PID loop
#define DEFAULT_Kp 18.06
#define DEFAULT_Ki 1.15
#define DEFAULT_Kd 70.97
#define PIDTEMPBED
#define MAX_BED_POWER 255 // limits duty cycle to bed; 255=full current
#define DEFAULT_bedKp 38.22
#define DEFAULT_bedKi 7.56
#define DEFAULT_bedKd 128.83
#define MAX_CHAMBER_POWER 255 // limits duty cycle to chamber heater; 255=full current
  #define PID_FUNCTIONAL_RANGE 10 // If the temperature difference between the target temperature and the actual temperature
  #define PID_EDIT_MENU         // Add PID editing to the "Advanced Settings" menu. (~700 bytes of flash)
  #define PID_AUTOTUNE_MENU     // Add PID auto-tuning to the "Advanced Settings" menu. (~250 bytes of flash)
#define PREVENT_COLD_EXTRUSION
#define EXTRUDE_MINTEMP 190
#define PREVENT_LENGTHY_EXTRUDE
#define EXTRUDE_MAXLENGTH 200
#define THERMAL_PROTECTION_HOTENDS // Enable thermal protection for all extruders
#define THERMAL_PROTECTION_BED     // Enable thermal protection for the heated bed
#define THERMAL_PROTECTION_CHAMBER // Enable thermal protection for the heated chamber
#define THERMAL_PROTECTION_COOLER  // Enable thermal protection for the laser cooling
#define USE_XMIN_PLUG
#define USE_YMIN_PLUG
#define USE_ZMIN_PLUG
#define ENDSTOPPULLUPS
#define X_MIN_ENDSTOP_INVERTING false // Set to true to invert the logic of the endstop.
#define Y_MIN_ENDSTOP_INVERTING false // Set to true to invert the logic of the endstop.
#define Z_MIN_ENDSTOP_INVERTING false // Set to true to invert the logic of the endstop.
#define I_MIN_ENDSTOP_INVERTING false // Set to true to invert the logic of the endstop.
#define J_MIN_ENDSTOP_INVERTING false // Set to true to invert the logic of the endstop.
#define K_MIN_ENDSTOP_INVERTING false // Set to true to invert the logic of the endstop.
#define X_MAX_ENDSTOP_INVERTING false // Set to true to invert the logic of the endstop.
#define Y_MAX_ENDSTOP_INVERTING false // Set to true to invert the logic of the endstop.
#define Z_MAX_ENDSTOP_INVERTING false // Set to true to invert the logic of the endstop.
#define I_MAX_ENDSTOP_INVERTING false // Set to true to invert the logic of the endstop.
#define J_MAX_ENDSTOP_INVERTING false // Set to true to invert the logic of the endstop.
#define K_MAX_ENDSTOP_INVERTING false // Set to true to invert the logic of the endstop.
#define Z_MIN_PROBE_ENDSTOP_INVERTING false // Set to true to invert the logic of the probe.
#define DEFAULT_AXIS_STEPS_PER_UNIT    { 640, 640, 400, 130.722 }
#define DEFAULT_MAX_FEEDRATE         { 100, 100, 12, 120 }
#define DEFAULT_MAX_ACCELERATION     { 500, 500, 100, 10000 }
#define DEFAULT_ACCELERATION          1000    // X, Y, Z ... and E acceleration for printing moves
#define DEFAULT_RETRACT_ACCELERATION  1000    // E acceleration for retracts
#define DEFAULT_TRAVEL_ACCELERATION   1000    // X, Y, Z ... acceleration for travel (non printing) moves
#define DEFAULT_EJERK    5.0  // May be used by Linear Advance
  #define JUNCTION_DEVIATION_MM 0.013 // (mm) Distance from real junction edge
  #define JD_HANDLE_SMALL_SEGMENTS    // Use curvature estimation instead of just the junction angle
#define S_CURVE_ACCELERATION
#define Z_MIN_PROBE_USES_Z_MIN_ENDSTOP_PIN
#define NOZZLE_TO_PROBE_OFFSET { 10, 10, 0 }
#define PROBING_MARGIN 10
#define XY_PROBE_FEEDRATE (133*60)
#define Z_PROBE_FEEDRATE_FAST (4*60)
#define Z_PROBE_FEEDRATE_SLOW (Z_PROBE_FEEDRATE_FAST / 2)
#define Z_CLEARANCE_DEPLOY_PROBE   10 // Z Clearance for Deploy/Stow
#define Z_CLEARANCE_BETWEEN_PROBES  5 // Z Clearance between probe points
#define Z_CLEARANCE_MULTI_PROBE     5 // Z Clearance between multiple probes
#define Z_PROBE_LOW_POINT          -2 // Farthest distance below the trigger-point to go before stopping
#define Z_PROBE_OFFSET_RANGE_MIN -20
#define Z_PROBE_OFFSET_RANGE_MAX 20
#define X_ENABLE_ON 0
#define Y_ENABLE_ON 0
#define Z_ENABLE_ON 0
#define E_ENABLE_ON 0 // For all extruders
#define DISABLE_X false
#define DISABLE_Y false
#define DISABLE_Z false
#define DISABLE_E false             // Disable the extruder when not stepping
#define DISABLE_INACTIVE_EXTRUDER   // Keep only the active extruder enabled
#define INVERT_X_DIR true
#define INVERT_Y_DIR true
#define INVERT_Z_DIR false
#define INVERT_E0_DIR false
#define INVERT_E1_DIR false
#define INVERT_E2_DIR false
#define INVERT_E3_DIR false
#define INVERT_E4_DIR false
#define INVERT_E5_DIR false
#define INVERT_E6_DIR false
#define INVERT_E7_DIR false
#define X_HOME_DIR -1
#define Y_HOME_DIR -1
#define Z_HOME_DIR -1
#define X_BED_SIZE 235
#define Y_BED_SIZE 235
#define X_MIN_POS 0
#define Y_MIN_POS -20
#define Z_MIN_POS 0
#define X_MAX_POS X_BED_SIZE
#define Y_MAX_POS Y_BED_SIZE
#define Z_MAX_POS 250
#define MIN_SOFTWARE_ENDSTOPS
  #define MIN_SOFTWARE_ENDSTOP_X
  #define MIN_SOFTWARE_ENDSTOP_Y
  #define MIN_SOFTWARE_ENDSTOP_Z
  #define MIN_SOFTWARE_ENDSTOP_I
  #define MIN_SOFTWARE_ENDSTOP_J
  #define MIN_SOFTWARE_ENDSTOP_K
#define MAX_SOFTWARE_ENDSTOPS
  #define MAX_SOFTWARE_ENDSTOP_X
  #define MAX_SOFTWARE_ENDSTOP_Y
  #define MAX_SOFTWARE_ENDSTOP_Z
  #define MAX_SOFTWARE_ENDSTOP_I
  #define MAX_SOFTWARE_ENDSTOP_J
  #define MAX_SOFTWARE_ENDSTOP_K
#define FILAMENT_RUNOUT_SENSOR
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

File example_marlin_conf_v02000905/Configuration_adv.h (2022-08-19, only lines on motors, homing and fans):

#define E0_AUTO_FAN_PIN -1
#define E1_AUTO_FAN_PIN -1
#define E2_AUTO_FAN_PIN -1
#define E3_AUTO_FAN_PIN -1
#define E4_AUTO_FAN_PIN -1
#define E5_AUTO_FAN_PIN -1
#define E6_AUTO_FAN_PIN -1
#define E7_AUTO_FAN_PIN -1
#define CHAMBER_AUTO_FAN_PIN -1
#define COOLER_AUTO_FAN_PIN -1
#define HOMING_BUMP_MM      { 5, 5, 2 }       // (mm) Backoff from endstops after first bump
#define HOMING_BUMP_DIVISOR { 2, 2, 4 }       // Re-Bump Speed Divisor (Divides the Homing Feedrate)
#define MICROSTEP_MODES { 16, 16, 16, 16, 16, 16 } // [1,2,4,8,16]
#define ADVANCED_PAUSE_FEATURE
  #define ADVANCED_PAUSE_PURGE_FEEDRATE        3  // (mm/s) Extrude feedrate (after loading). Should be slower than load feedrate.
  #define ADVANCED_PAUSE_PURGE_LENGTH         25  // (mm) Length to extrude after loading.
  #define ADVANCED_PAUSE_RESUME_PRIME          0  // (mm) Extra distance to prime nozzle after returning from park.

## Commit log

2022-08-01 add sch pcb and source code
    [Sheet1.SchDoc]
2022-08-02 add bom.xls layout pdf
    [MMU2S_HW_BOM.xlsx]
2022-08-02 new switch_board and some imges
    [PCB1.PcbDoc, switch_board.PrjPcb]
2022-08-02 更改目录
    [MMU2S_HW_BOM.xlsx, Sheet1.SchDoc]
2022-08-02 优化走线
2022-08-03 更改配料表元件数量
    [MMU2S_HW_BOM.xlsx]
2022-08-18 1:更新marlin配置示例 2:更改mmu源代码.减慢退料速度
    [Configuration.h, Configuration_adv.h]
2022-08-18 add marlin pin map
2022-08-18 old version gerber file
2022-08-18 change file name
    [Sheet1_V4.1.SchDoc]
2022-08-19 加入按键操作说明
2022-08-19 修复bom表错误
    [MMU2S_HW_BOM.xlsx]
2022-08-19 加入串口电平选择说明
2022-08-19 更改mmu配置,减小挤压距离
    [Configuration.h, Configuration_adv.h]
2022-08-19 加入V4.1串口示意图
2022-08-19 优化走线 usb
2022-08-20 电机接线示意
2022-08-20 板框底示意图
2022-08-21 供电示意图
2022-08-21 加入使用教程
2022-08-22 焊接说明
2022-08-22 marlin 设置文件主要变更说明
2022-08-23 按键小板接线图
2022-08-25 更改使用教程送料管长度调整,准确的校准示例
2022-08-27 加入切片示例
2022-08-27 加入新的图片
2022-08-27 增加V3.4接线图
2022-08-27 补充开关小板接线图
    [MMU2S_HW_BOM.xlsx]
2022-08-27 更新使用教程 设置菜单指引
2022-08-31 替换程序,减小噪音
2022-12-15 修改注释错误
2022-12-15 修改参数

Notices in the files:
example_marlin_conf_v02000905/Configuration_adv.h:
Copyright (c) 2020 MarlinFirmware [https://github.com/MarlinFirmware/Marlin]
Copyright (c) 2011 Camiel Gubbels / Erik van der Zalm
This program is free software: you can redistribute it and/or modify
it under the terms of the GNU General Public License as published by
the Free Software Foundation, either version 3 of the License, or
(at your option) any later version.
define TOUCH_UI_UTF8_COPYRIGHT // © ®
